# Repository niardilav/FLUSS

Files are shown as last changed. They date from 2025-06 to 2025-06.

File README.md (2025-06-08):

# Proyecto FLUSS
EL proyecto FLUSS busca investigar la viabilidad de turbinas tipo savonious de eje horizonal en los rios de montaña de colombia, y se busca desarrollar un prototipo de turbina para uso en laboratorio.

En este repositorio se encuentran los avances del proyecto FLUSS ganador de la convocatoria "Ingenio que transforma" 2024, cada carpeta corresponde a un desarrollo llevadoa a cabo durante la convocatoria, en las carpetas se pueden encontrar los archivos de códigos, modelos CAD y datos crudos de laboratorio.

A la fecha el proyecto se encuentra en desarrollo y se han logrado implementar pruebas de laboratorio para turbinas savonious en aire y se ha diseñado un banco de pruebas de generadores para caracterizar un motor stepper como generador.

## Participación en eventos cientificos

3 ponencias en el CIMM XII
- DISEÑO Y PROTOTIPADO DE UN TÚNEL DE VIENTO PARA PRUEBAS A ESCALA DE TURBINAS TIPO SAVONIUS. 
- CALIBRACIÓN Y USO DE GALGAS EXTENSIOMÉTRICAS.
- BANCO DE PRUEBAS PARA LA CARACTERIZACIÓN DE MOTORES COMO GENERADORES.

1 poster en expotech-UNAD 2025    
- Análisis del comportamiento de una turbina Savonius en condiciones de superficie libre.

# Integrantes del proyecto
Estudiantes

- Nicolás Ardila Vergara 
  Estudiante Ing Mecánica UNAL
  Lider del proyecto
  niardilav@unal.edu.co

- Mateo Velandia Suarez 
  Estudiante Ing Mecánica UNAL
  mavelandias@unal.edu.co
  
- Jairo David Diaz Luna
  Estudiante Ing Mecatrónica UNAL
  jdiazlu@unal.edu.co
  
- Maria Lucia Arias Ortiz
  Estudiante Ing Mecatrónica UNAL
  mariasor@unal.edu.co
  
- Laura Catalina Ramirez Villareal
  Estudiante Ing Mecánica UNAL
  laramirezvi@unal.edu.co
  
- Juan Jose Benavides Garreta
  Estudiante Ing Mecánica UNAL

- Juan Sebastian Moreno Gonzalez
  Estudiante Ing Electronica UNAL

- Jaime Andres Martín Moreno
  Estudiante Ing Mecatrónica UNAL

- Jonathan David Rodriguez Larrota
  Estudiante Ing Electrica UNAL

### Director del proyecto
Juan Miguel Mantilla Gonzalez
  jmmantillag@unal.edu.co
### Codirector del proyecto
Nestor Alonso Mancipe Muños

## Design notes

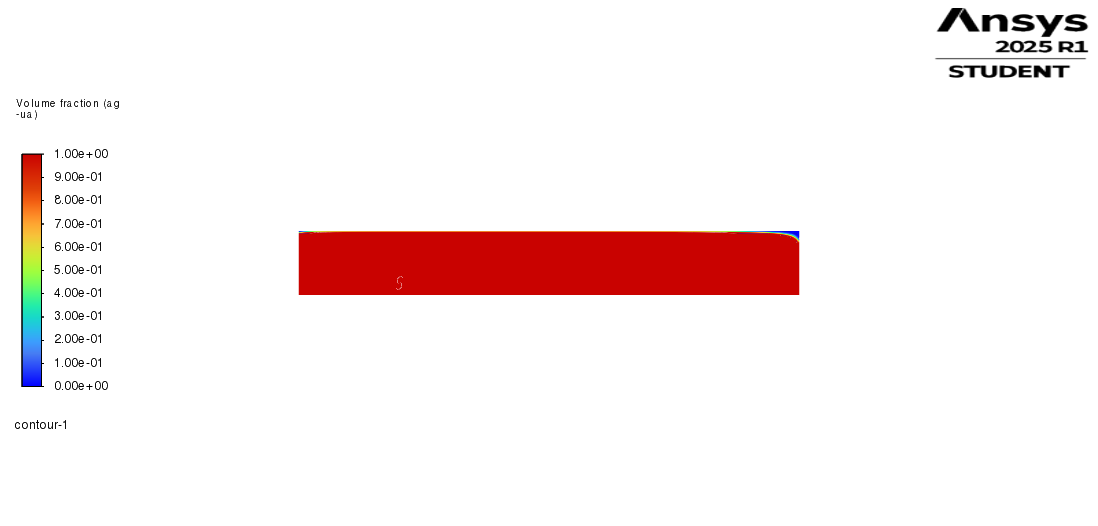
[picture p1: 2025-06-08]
Simulaciones_Canal_Hidraulica/Simulaciones_Ansys_y postproceso/turbina22_files/progress_files/dp0/FFF/Fluent/contour-1.png

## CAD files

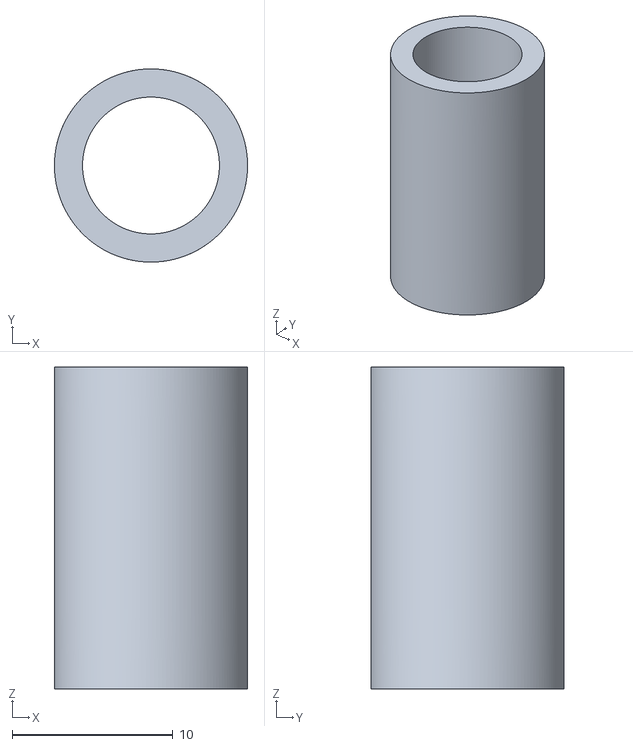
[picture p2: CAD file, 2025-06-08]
Pruebas_tunel_de_viento/Tunel_FLUSS/Modelos_inventor/Ensamble inercia/Camisa_eje.stl
12.0 x 12.0 x 20.0

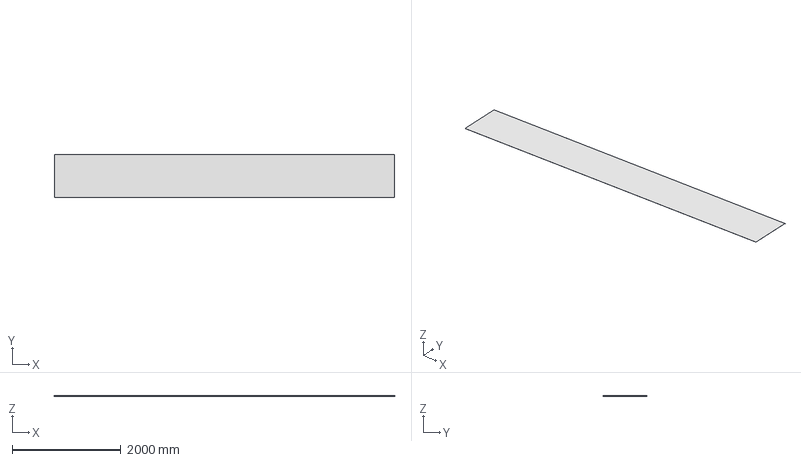
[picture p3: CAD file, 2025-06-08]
Simulaciones_Canal_Hidraulica/Simulaciones_Ansys_y postproceso/turbina22_files/import_files/TunelBasicoParte1norejas.stp
6260.0 x 800.0 x 1.00 mm

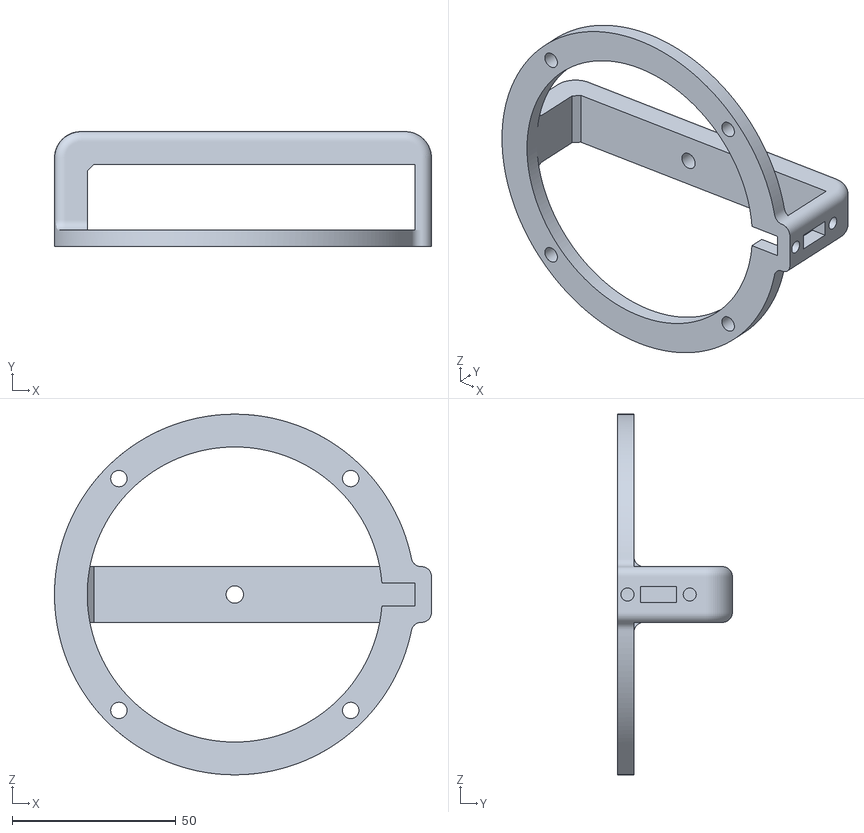
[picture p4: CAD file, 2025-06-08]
Pruebas_tunel_de_viento/Tunel_FLUSS/Modelos_inventor/Ensamble inercia/Soporte.stl
115.0 x 35.0 x 110.0

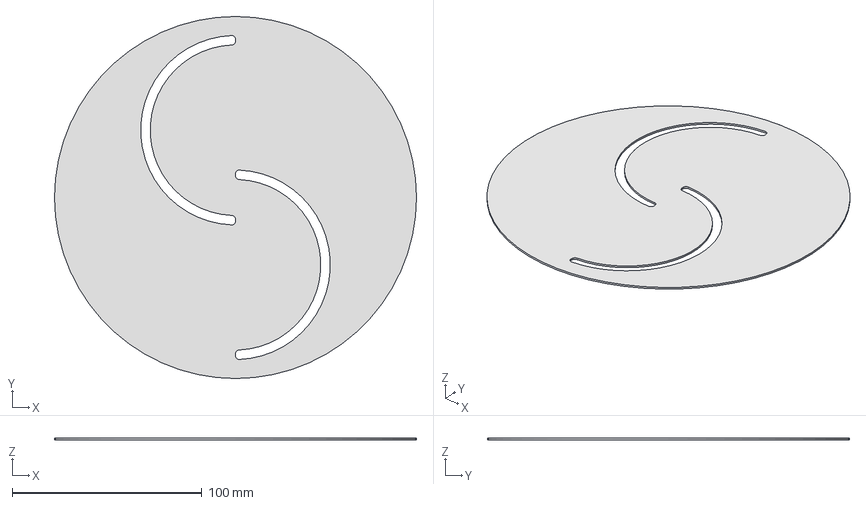
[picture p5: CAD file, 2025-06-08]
Simulaciones_Canal_Hidraulica/Simulaciones_Ansys_y postproceso/turbina22_files/import_files/TunelBasicoParte2.stp
191.0 x 191.0 x 1.00 mm

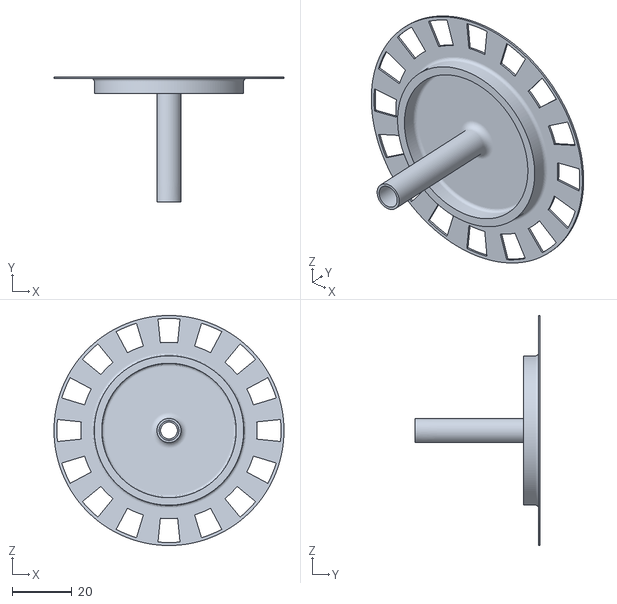
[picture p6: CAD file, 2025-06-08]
Pruebas_tunel_de_viento/Tunel_FLUSS/Modelos_inventor/Ensamble inercia/Eje_econder_V2.stl
77.0 x 42.0 x 77.0

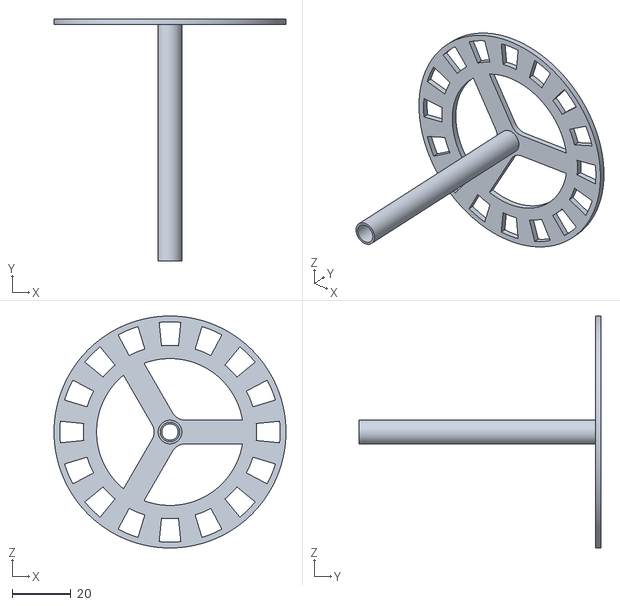
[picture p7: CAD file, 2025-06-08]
Pruebas_tunel_de_viento/Tunel_FLUSS/Modelos_inventor/Ensamble inercia/Eje_econder.stl
79.0 x 82.5 x 79.0

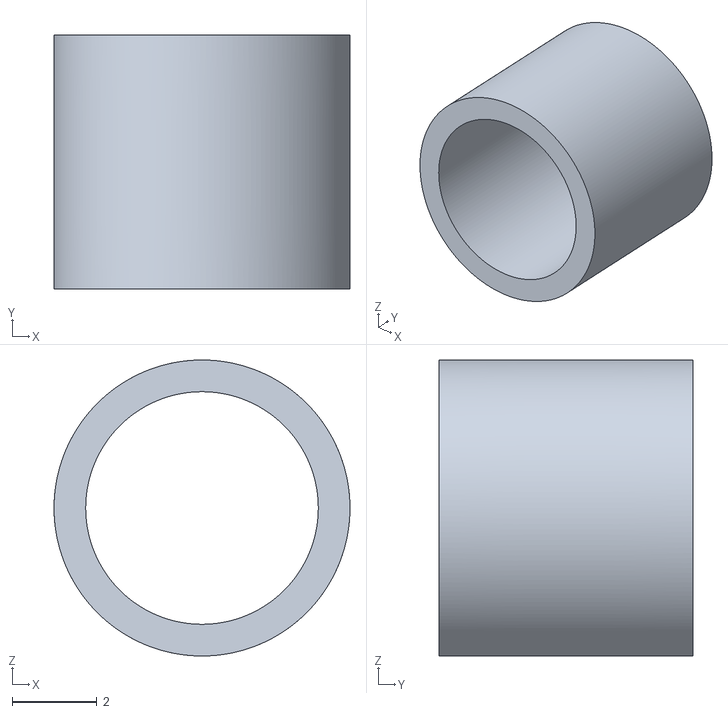
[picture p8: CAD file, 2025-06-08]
Pruebas_tunel_de_viento/Tunel_FLUSS/Modelos_inventor/Ensamble inercia/Buje_inercia.stl
7.00 x 6.00 x 7.00

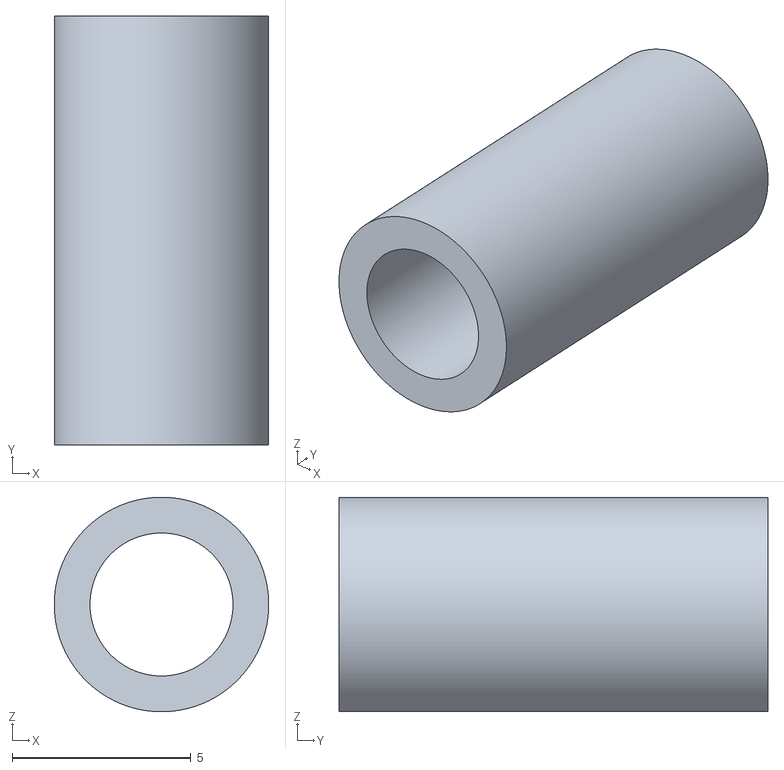
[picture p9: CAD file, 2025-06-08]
Pruebas_tunel_de_viento/Tunel_FLUSS/Modelos_inventor/Ensamble inercia/Poste_sensor.stl
6.00 x 12.0 x 6.00

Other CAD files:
Pruebas_tunel_de_viento/Tunel_FLUSS/Modelos_inventor/Ensamble inercia/Buje_inercia.ipt
Pruebas_tunel_de_viento/Tunel_FLUSS/Modelos_inventor/Ensamble inercia/Eje_econder.ipt
Pruebas_tunel_de_viento/Tunel_FLUSS/Modelos_inventor/Ensamble inercia/OldVersions/Eje_econder.0003.ipt
Pruebas_tunel_de_viento/Tunel_FLUSS/Modelos_inventor/Ensamble inercia/OldVersions/Prueba_ensamble inercia.0001.iam
Pruebas_tunel_de_viento/Tunel_FLUSS/Modelos_inventor/Ensamble inercia/OldVersions/Seccion_tunel.0001.ipt
Pruebas_tunel_de_viento/Tunel_FLUSS/Modelos_inventor/Ensamble inercia/OldVersions/Sensor.0002.ipt
Pruebas_tunel_de_viento/Tunel_FLUSS/Modelos_inventor/Ensamble inercia/OldVersions/Soporte.0001.ipt
Pruebas_tunel_de_viento/Tunel_FLUSS/Modelos_inventor/Ensamble inercia/OldVersions/soporte motor.0001.ipt
Pruebas_tunel_de_viento/Tunel_FLUSS/Modelos_inventor/Ensamble inercia/Part20.ipt
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

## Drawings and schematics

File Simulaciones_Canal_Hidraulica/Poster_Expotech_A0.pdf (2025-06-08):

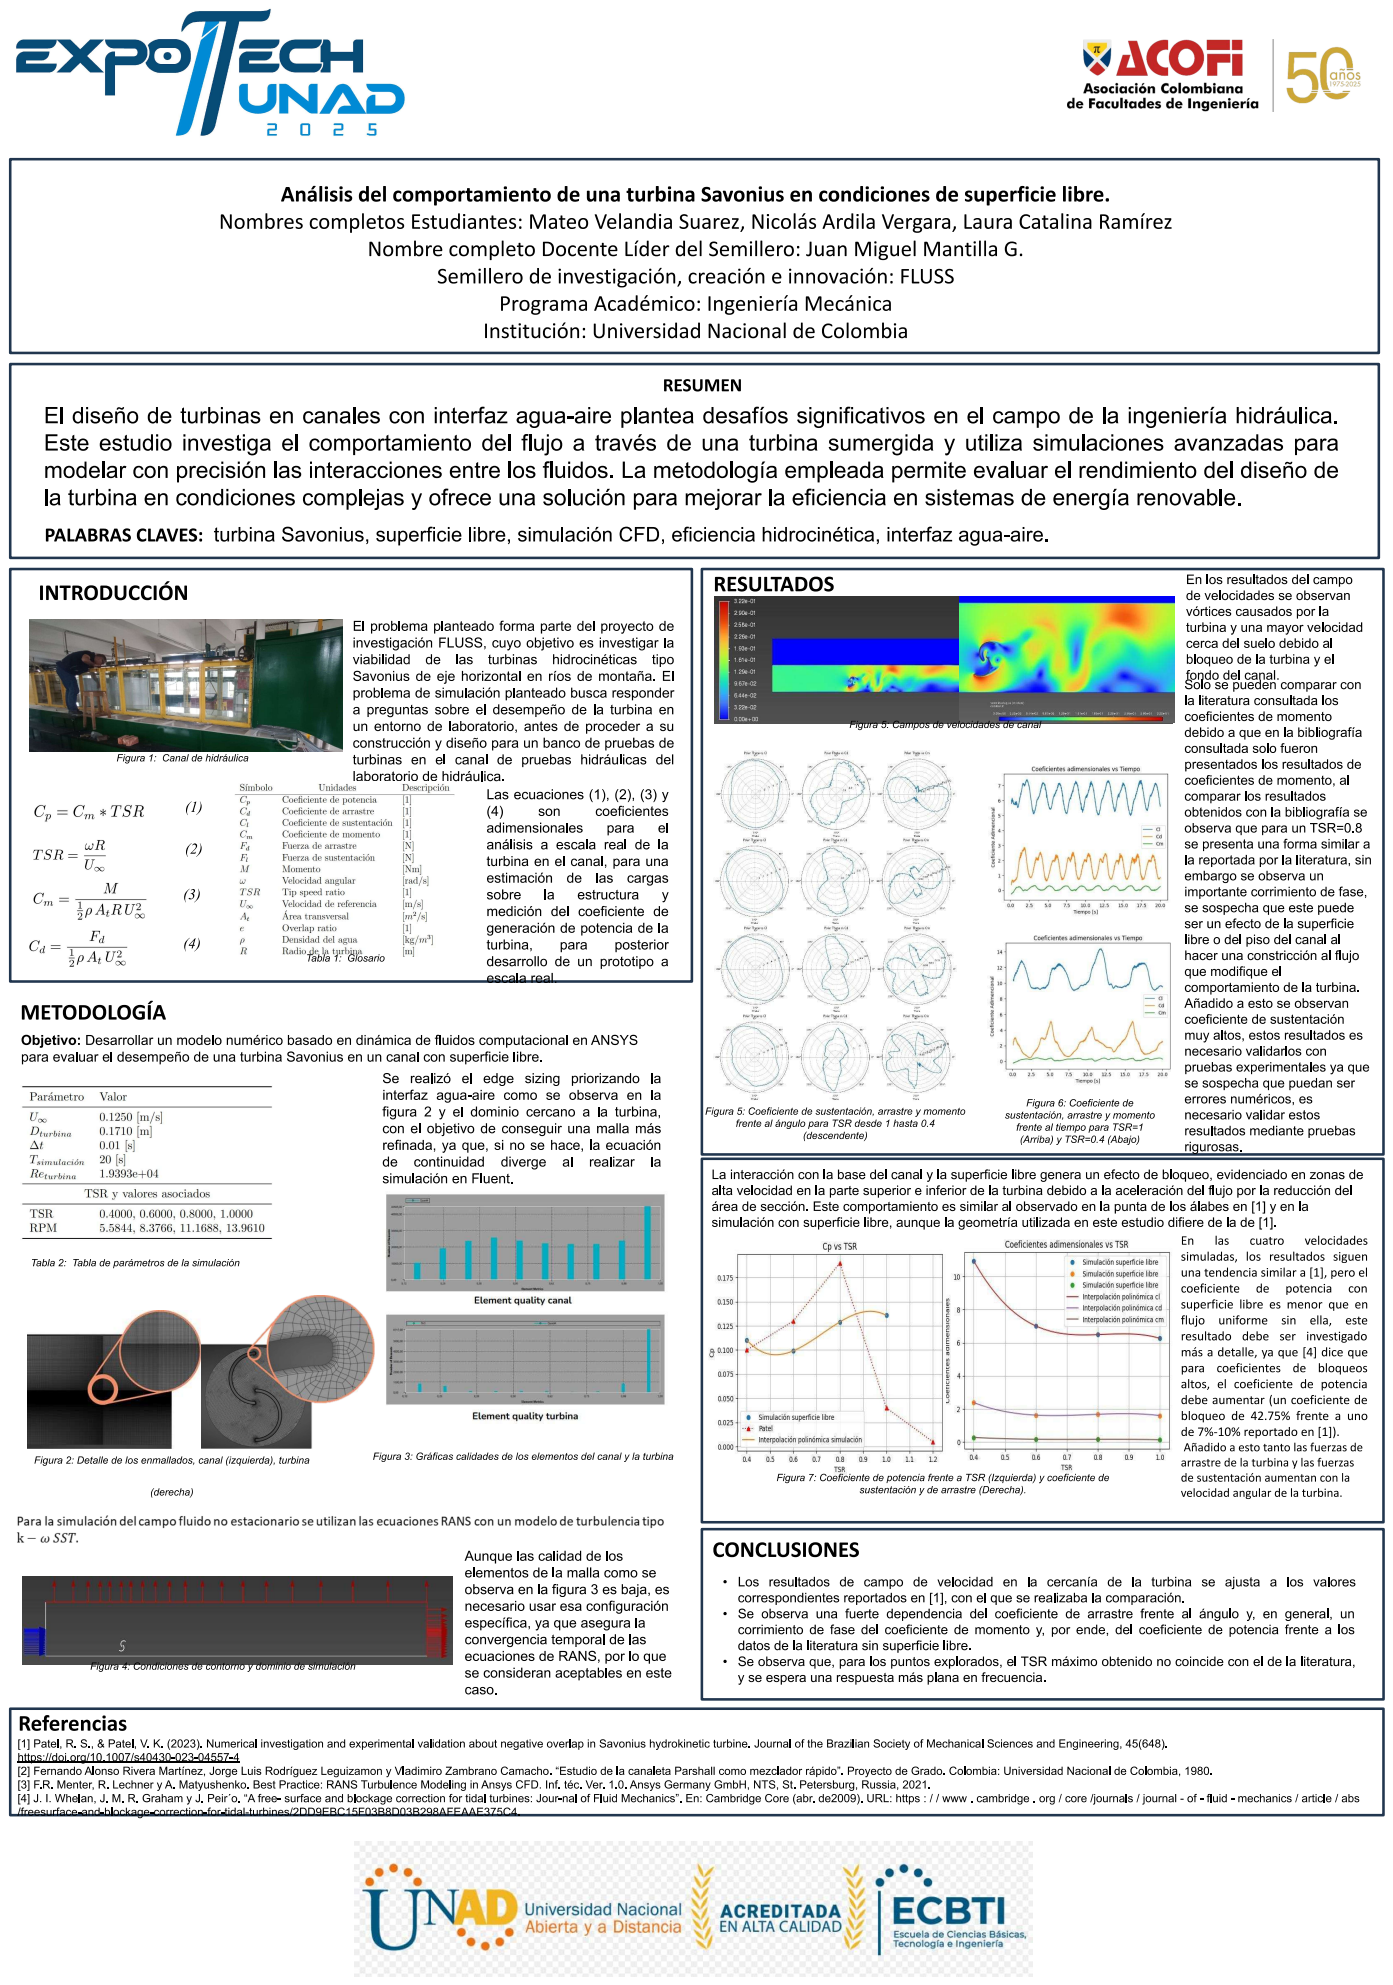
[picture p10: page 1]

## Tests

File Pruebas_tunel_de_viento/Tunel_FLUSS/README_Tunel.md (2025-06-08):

# Experimentos de similitud dimensional en tunel de viento
En esta carpeta se incluyen los diseños del tunel de viento de FLUSS, el trabajo presentado al CIMM y carpetas con datos crudos de pruebas de laboratorio junto con códigos de procesamiento de datos para la generación de las curvas de desempeño de la turbina.

Los datos crudos fueron generados en el tunel de viento propio para una turbina de 50mm de diametro, OR=-0.17 AR=1, y los settings del ESC del tunel fuerin 22V a 1.230 ms de Ton en la señal de PWM, en una fuente dual de 60W. La velocidad de viento medida oscila entre 7 y 8 m/s en la entrada de la turbina.

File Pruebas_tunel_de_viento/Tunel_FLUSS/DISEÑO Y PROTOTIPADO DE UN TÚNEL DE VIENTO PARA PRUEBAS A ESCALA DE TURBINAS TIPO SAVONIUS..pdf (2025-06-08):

## DISEÑO Y PROTOTIPADO DE UN TÚNEL DE VIENTO PARA

PRUEBAS A ESCALA DE TURBINAS TIPO SAVONIUS.

Nicolás Ardila Vergara, Mateo Velandia Suarez, Laura Catalina Ramírez Villarreal, Juan José Benavides Garreta, Maria Lucia Arias Ortiz, Jonathan David Rodriguez Larrota, Jaime Andrés Martín Moreno, Jairo David Diaz Luna, Juan Sebastian Moreno Gonzalez.

Proyecto “FLUSS” código Hermes (62804), Universidad Nacional de Colombia, Colombia. Núcleo Temático: Energías renovables y fuentes no convencionales.

### Introducción

En la actualidad es campo de investigación el uso de turbinas hidrocinéticas tipo savonius para la producción energética, ya sea para aprovechar la energía de ríos o ayudar a mitigar los efectos del cambio climático. Dado que la turbina está inmersa en un fluido, es necesario hacer todo el análisis hidrodinámico que esto conlleva. Por está razón el presente trabajo aborda el diseño y construcción de un túnel de viento, para la caracterización hidrodinámica de este tipo de turbinas.

Palabras clave: turbina, hidrocinética, savonius, túnel de viento.

### Métodos

Por simplicidad de construcción y las restricciones de espacio se decidió construir un túnel de viento tipo abierto de sección cuadrada, donde se incluye una admisión tobera, laminarizador, la sección de prueba y un difusor. El ventilador se encuentra en la parte posterior del difusor. El túnel tiene como objetivo en el corto plazo poder medir fuerzas de arrastre y en el futuro fuerzas de sustentación y momentos.
Para el diseño del túnel se usó la ecuación (1) para pérdidas menores y mayores para ductos, donde se tuvo en cuenta la longitud de la sección de prueba del túnel de viento, el difusor, la tobera, la admisión y el laminarizador.

Esto con el fin de evaluar el desempeño del túnel previo a su construcción y determinar los parámetros geométricos que permitan un mayor desempeño. Los parámetros para las pérdidas menores fueron tomados de [Karassik, 2004], [McGill, 2003], [White, 2004] y para la sección de prueba se utilizó el factor de fricción de Darcy para la rugosidad de maderas lisas [White, 2004].

En la Figura 1 se muestra la curva de desempeño del túnel de viento calculada y el punto de operación para el ventilador seleccionado a una

velocidad fija. Cómo ventilador se usó una hélice de avión de radio control propulsada por un motor

brushless por su alta relación entre potencia y tamaño.

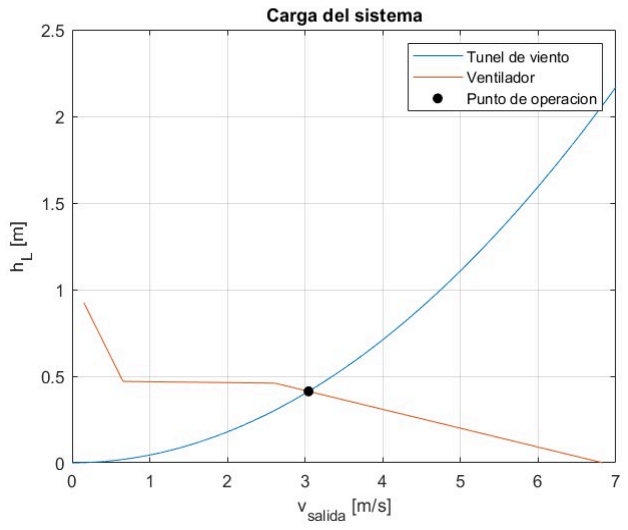
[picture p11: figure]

Figura 1: Punto de operación del sistema.

Para verificar el correcto funcionamiento del túnel se decidió realizar experimentos del coeficiente de arrastre de una geometría simple como lo es una esfera, visualizar el flujo con vapores de glicerina, y el perfil de velocidades dentro del túnel con un anemómetro de hilo caliente. Además se instalarán manómetros diferenciales de alcohol para medir las caídas de presiones en las secciones del túnel.

### Resultados

En la figura 2 se observa el primer prototipo del túnel de viento. El túnel tiene diferentes agujeros para inserción de aparatos de medición, En la sección de prueba se posiciona una celda de carga acoplada al soporte donde irá el objeto de prueba. En la parte de arriba del túnel se encuentra el sistema de control del motor y la celda de carga para la medición de la fuerza de arrastre.

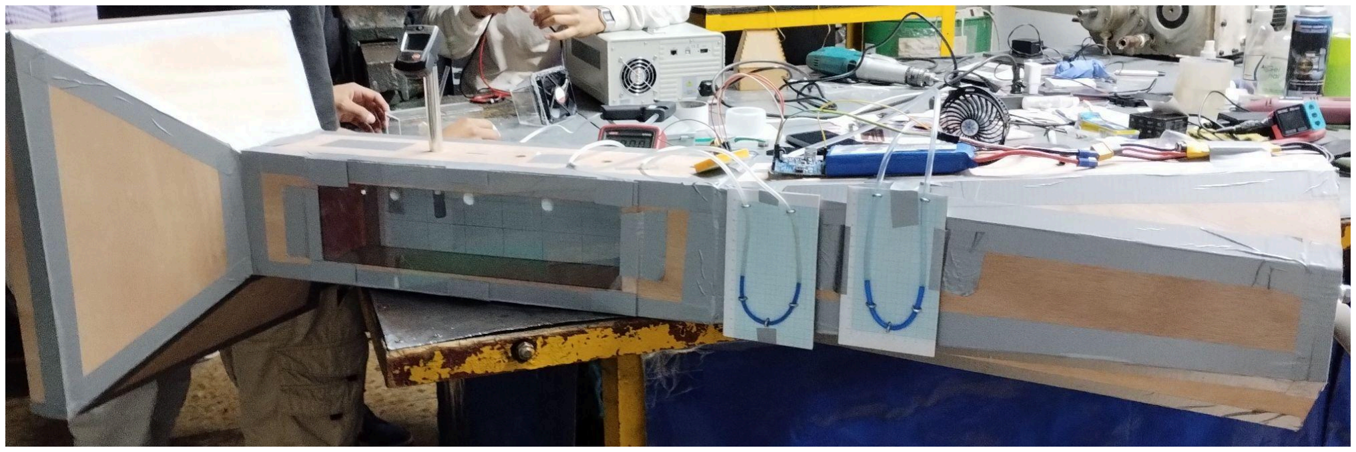
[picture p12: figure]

Figura 2: Primer prototipo del túnel de viento siendo calibrado.

En la figura 3 se observa las curvas resultado para coeficientes de arrastre teórico para una esfera lisa, los puntos obtenidos experimentalmente , y la curva de ajuste del resultado experimental.

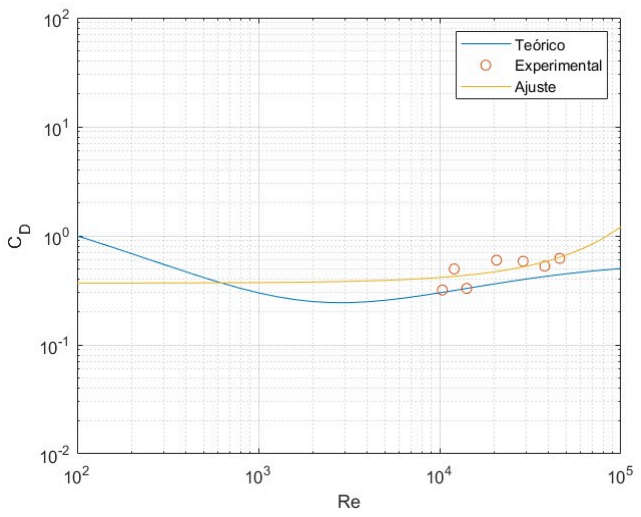
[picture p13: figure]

Figura 3: Coeficiente de arrastre contra número de Reynolds.

### Discusión

A las rangos de Reynolds medidos los datos de coeficiente de arrastre para la esfera se acercan a los teóricos, se observa una tendencia similar pero con arrastres mayores a la esfera lisa, esto es de esperar por la rugosidad inherente a la esfera real. Por lo tanto se verifica el correcto funcionamiento del túnel en el rango de números de Reynolds de
1x 10 a | .

4
4 x 10

4

El objetivo del túnel es modelar los coeficientes de arrastre, sustentación y momento para una turbina savonius que operará en un rango de números de
Reynolds entre 2. 2 x 10 a | el túnel fue

5
6 x 10

5
capaz de generar velocidades dentro de este rango pero se encuentra limitado por el tiempo de descarga de la batería del motor se espera realizar en el futuro más experimentos para validar el funcionamiento del túnel en este régimen de flujo, sin embargo si no fuera viable aumentar el rango de funcionamiento del túnel muchas geometrías presentan cambios significativos en sus coeficientes de arrastre y sustentación luego de Re > 10

4
[White, 2004], por lo cual no se descarta su uso para experimentación en las turbinas Savonius.

### Referencias

Karassik et al., Pump handbook, McGraw-Hill, 2004.

McGill, Duct System Design Guide, Air-Flow Corporation, 2003.

White et al., Mecánica de Fluidos, 5ta Edición, McGraw-Hill/Interamericana de España, S.A.U., 2004.

### Agradecimientos

Este trabajo fue financiado por la unidad de gestión de la innovación Ingnova de la Universidad Nacional de Colombia bajo la convocatoria Ingenio que transforma 2024, y a los docentes investigadores directores del Proyecto Fluss Juan Miguel Mantilla y Nestor Alonso Mancipe.

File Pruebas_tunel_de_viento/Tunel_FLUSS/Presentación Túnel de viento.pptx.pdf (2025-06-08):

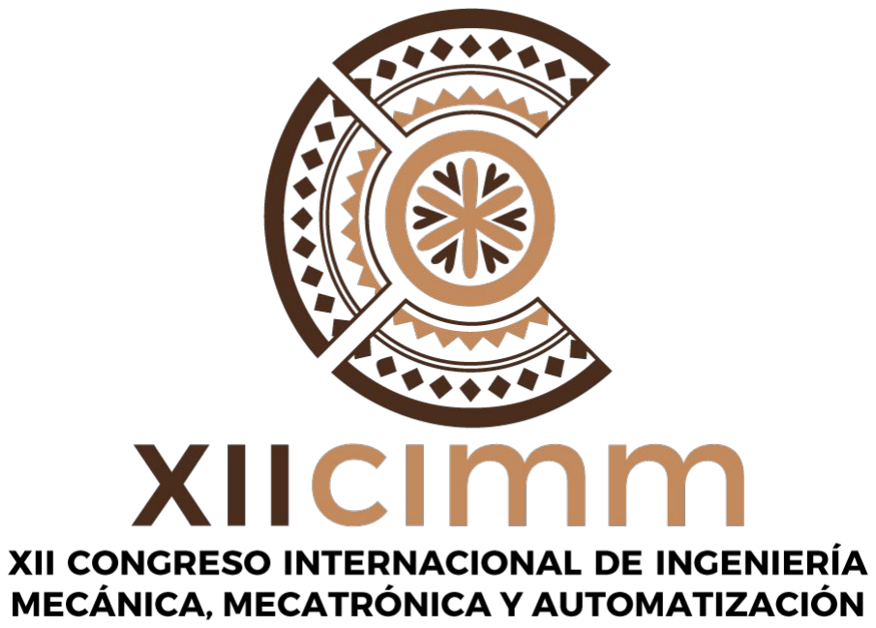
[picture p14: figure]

DISEÑO Y PROTOTIPADO DE UN TÚNEL DE VIENTO PARA PRUEBAS A ESCALA DE TURBINAS TIPO SAVONIUS

Autores:
Nicolas Ardila Vergara, Juan José Benavides Garreta, Laura Catalina Ramirez Villarreal, Mateo Velandia Suarez

Proyecto “FLUSS”
Código Hermes 62804

Universidad Nacional De Colombia, Colombia Núcleo Temático: Energías renovables y fuentes no convencionales.

INTRODUCCIÓN

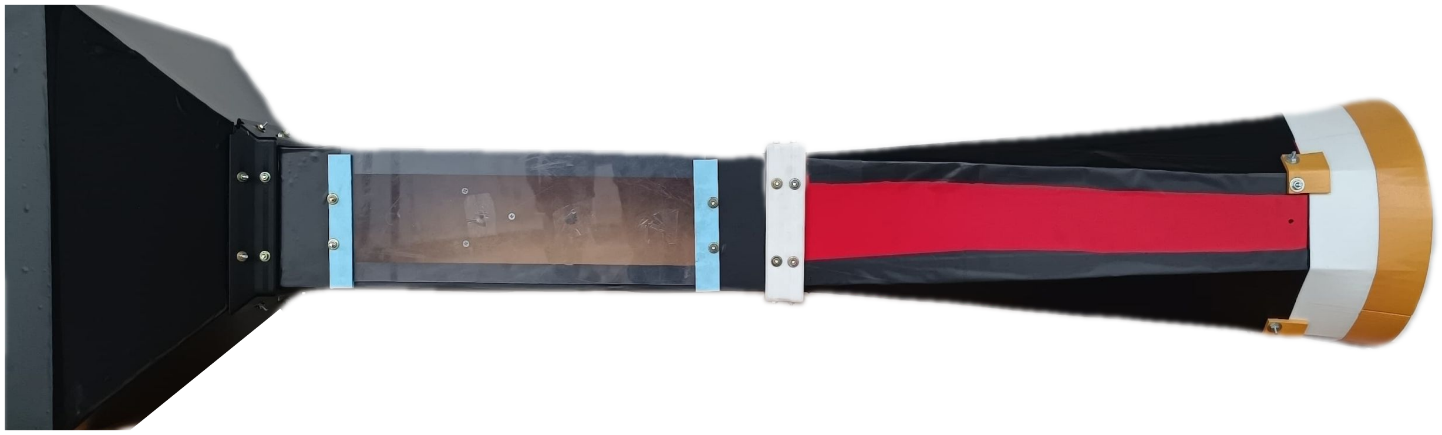
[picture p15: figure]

PROBLEMÁTICA

Con el fin de ahondar más a fondo la investigación de las turbinas tipo Savonius, se desarrolló un túnel de viento para la caracterización hidrodinámica de las mismas.

PALABRAS CLAVE:
Turbina, hidrocinética, savonius, túnel de viento.

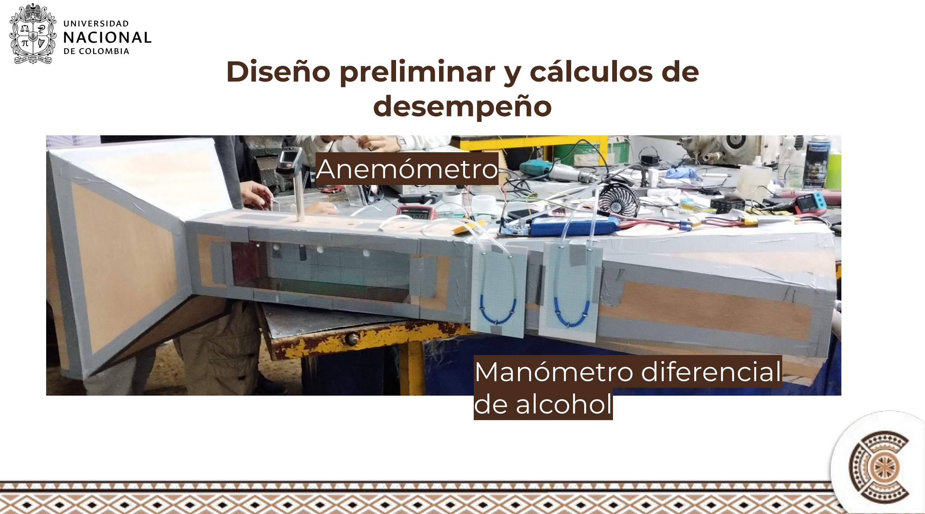
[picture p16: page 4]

Diseño preliminar y cálculos de desempeño

Anemómetro

Manómetro diferencial
de alcohol

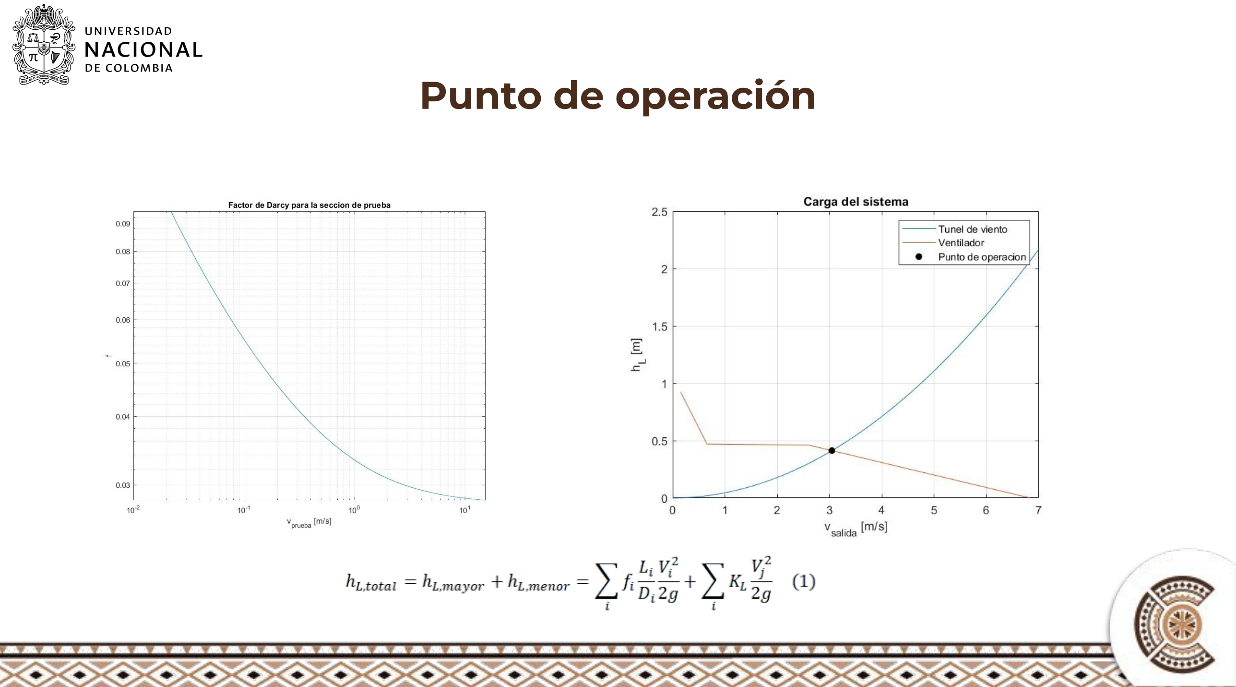
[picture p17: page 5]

Punto de operación

Capa limite

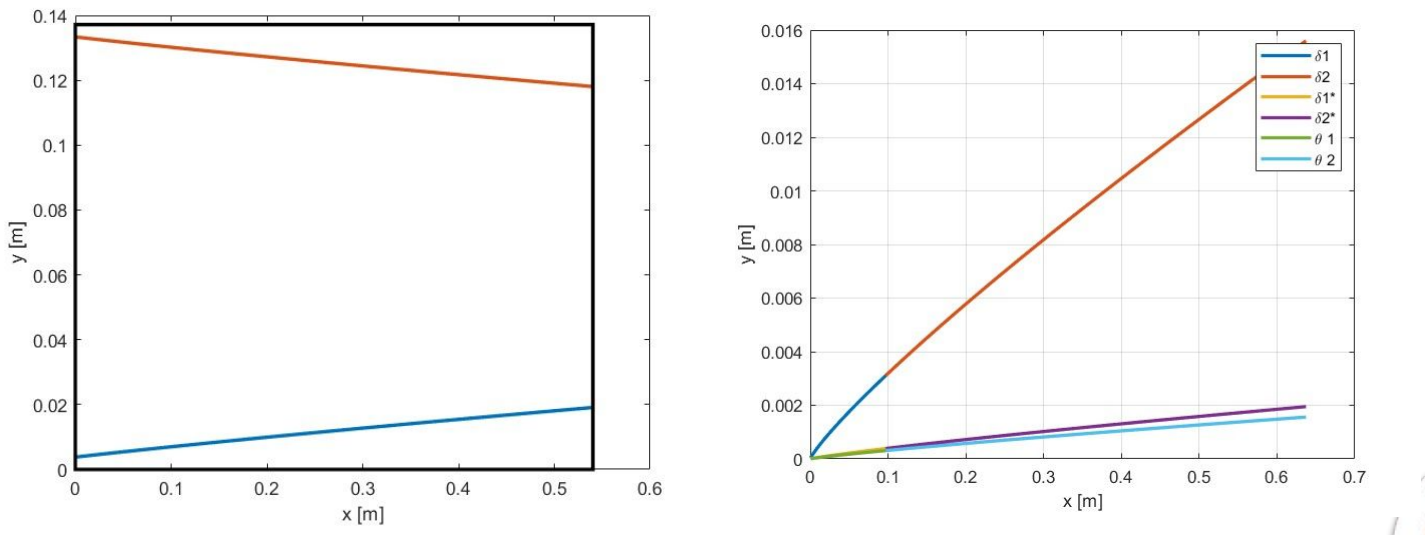
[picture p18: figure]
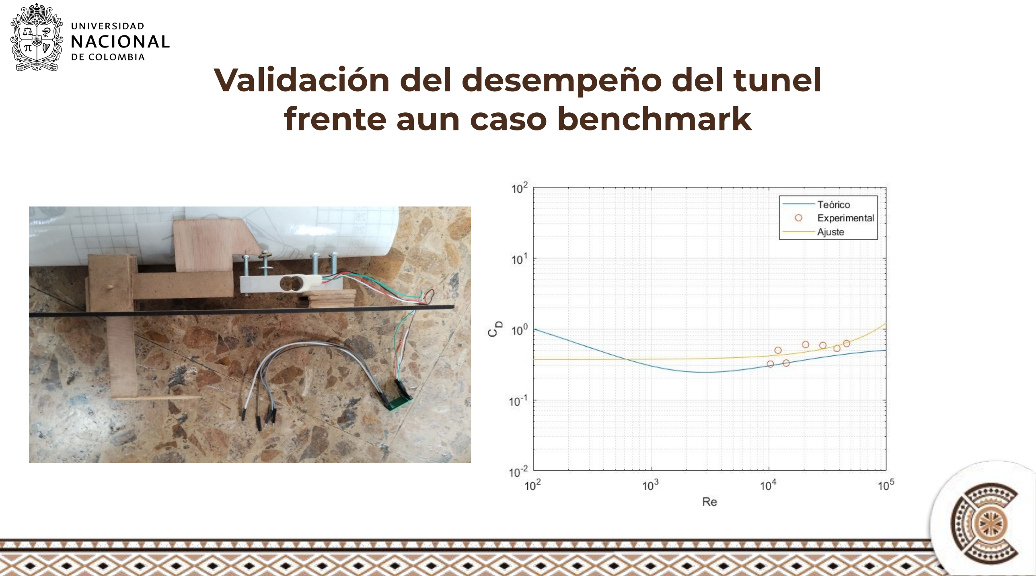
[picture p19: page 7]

Validación del desempeño del tunel frente aun caso benchmark

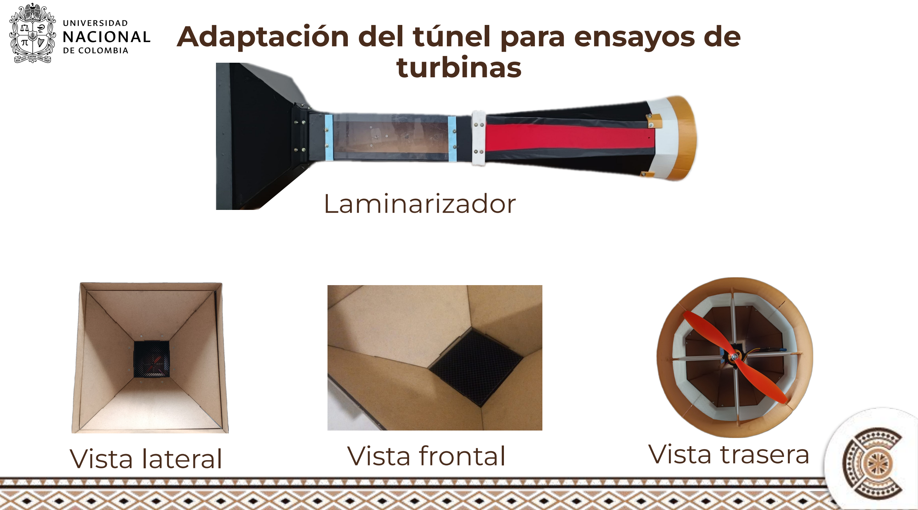
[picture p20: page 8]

Adaptación del túnel para ensayos de turbinas

Laminarizador

Vista lateral | Vista frontal | Vista trasera


Setup experimental

Osciloscopio

Generador de señales

Fuente de poder

Soporte motor


Montaje de la turbina

Turbinas savonius AR 1 ½ y ⅓ | Montaje de la turbina en el túnel


Refrigeración y modificación del ESC


Adaptación del túnel para funcionamiento

Rueda de inercia y encoder

Arduino para
adquisiscion de datos

Turbina en operación


Propuesta de modelo dinámico de la turbina

Propuesta de modelo dinámico de la turbina


Resultados
Primeros ensayos

https://youtu.be/QMdxYg5zm-o?si=KOCj9dZmcQfAikXl

https://youtu.be/QMdxYg5zm-o?si=dhmz1Cvq0xyAbkyk | https://youtu.be/QMdxYg5zm-o?si=KOCj9dZmcQfAikXl

Resultados
Primeros ensayos

https://youtu.be/QMdxYg5zm-o?si=KOCj9dZmcQfAikXl


https://youtu.be/KIURfHuR08Y?si=ImleQsb3eJ62W4uU&t=11


RESULTADOS


RESULTADOS
Operación del túnel


RESULTADOS
Primer ensayo de la turbina


RESULTADOS
Primer ensayo de la turbina


RESULTADOS
Primer ensayo de la turbina

RESULTADOS
Primer ensayo de la turbina


CONCLUSIONES

Se requieren más experimentos para poder trazar una curva más cercana a la teórica.

Se deben implementar sistemas para bajar la fricción con el objetivo de aumentar el TSR y poder trazar una región mayor de la curva.

Es necesario la implementación de un sistema de adquisición de datos con mayor frecuencia de muestreo.

TRABAJO A FUTURO

- Mejoras del sistema de adquisición de datos del túnel de viento.
- Utilización de una fuente de poder más potente para obtener velocidades más altas en el túnel de viento.
- Realizado de las curvas de desempeño de la turbina prototipo con corrección de fricción.

AGRADECIMIENTOS

Este trabajo fue financiado por la unidad de gestión de la innovación Ingnova de la Universidad Nacional de Colombia bajo la convocatoria Ingenio que transforma 2024, y a los docentes investigadores directores del Proyecto “Fluss” Juan Miguel Mantilla y Néstor Alonso Mancipe.

Contacto:
niardilav@unal.edu.co
+57 3187628596

REFERENCIAS


- J. B. Barlow, W. H. Rae Jr., and A. Pope, Low-Speed Wind Tunnel Testing, 3rd. John Wiley Sons, Inc., 1999.
- Karassik et al., Pump handbook, McGraw-Hill, 2004.
- McGill, Duct System Design Guide, Air-Flow Corporation, 2003.
- White et al., Mecánica de Fluidos, 5ta Edición, McGraw-Hill/Interamericana de España, S.A.U., 2004.

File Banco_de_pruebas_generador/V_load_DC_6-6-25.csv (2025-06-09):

Ohm @ 2ms-12V | Vload 1 | Vload 2 | Vload 3 | freq 1 | freq 2 | freq 3
100 | 13.77 | 13.43 | 13.36 | 2758 | 2764 | 2763
200 | 23.62 | 23.6 | 24.1 | 2650 | 2650 | 2647
300 | 30.11 | 29.75 | 29.72 | 2609 | 2610 | 2610
400 | 33.7 | 33.68 | 33.67 | 2602 | 2602 | 2601
500 | 36.37 | 36.35 | 36.35 | 2609 | 2608 | 2608
600 | 38.3 | 38.28 | 38.27 | 2619 | 2620 | 2620
700 | 39.71 | 39.72 | 39.72 | 2631 | 2632 | 2632
800 | 40.8 | 40.8 | 40.81 | 2640 | 2640 | 2640
900 | 41.68 | 41.7 | 41.69 | 2649 | 2649 | 2649
1000 | 42.46 | 42.46 | 42.26 | 2657 | 2657 | 2657

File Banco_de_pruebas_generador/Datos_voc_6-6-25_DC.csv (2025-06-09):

ms @ 12V | Voc 1 | Voc 2 | Voc 3 | freq 1 | freq 2 | freq 3
1.1 | 3.263 | 3.252 | 3.252 | 209 | 209 | 209.7
1.2 | 11.13 | 11.13 | 11.13 | 655 | 655 | 655
1.3 | 19.19 | 19.18 | 19.18 | 976 | 976 | 976
1.4 | 24.15 | 24.16 | 24.17 | 1286 | 1286 | 1286
1.5 | 33.68 | 33.59 | 33.78 | 1592 | 1592 | 1596
1.6 | 44.59 | 44.6 | 44.64 | 1890 | 1890 | 1891
1.7 | 57.3 | 57.4 | 57.3 | 2176 | 2176 | 2175
1.8 | 71.6 | 71.7 | 71.7 | 2454 | 2454 | 2454
1.9 | 83.6 | 83.7 | 83.7 | 2697 | 2698 | 2698
2 | 87.1 | 87.1 | 87.1 | 2776 | 2776 | 2776

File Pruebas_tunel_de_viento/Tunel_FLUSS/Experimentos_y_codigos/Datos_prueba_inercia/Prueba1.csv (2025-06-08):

#! | Workbook: | Custom | Custom
#! | Para reproducir estos datos: abra el archivo original de Excel | haga clic en el botón *Importar archivo de datos* de la pestaña *Secuencia de datos* de la cinta de opciones y desplácese hasta este archivo.
#! | Para obtener más información | visite http://aka.ms/hackingstem/
1902156 | 0
1902168 | 0
1902180 | 0
1902191 | 0
1902202 | 0
1902214 | 0
1902225 | 0
1902236 | 0
1902248 | 1
1902260 | 1
1902271 | 1
1902282 | 1
1902294 | 1
1902305 | 1
1902317 | 1
1902328 | 1
1902340 | 1
1902351 | 1
1902362 | 1
1902374 | 1
1902386 | 1
1902397 | 0
1902408 | 0
1902419 | 0
1902431 | 0
1902443 | 0
1902454 | 0
1902466 | 0
1902477 | 0
1902488 | 0
1902499 | 0
1902512 | 0
1902523 | 0
1902534 | 0
1902545 | 0
1902557 | 1
1902568 | 0
1902580 | 0
1902592 | 0
1902603 | 0
1902614 | 0
1902625 | 0
1902637 | 0
1902649 | 0
1902660 | 0
1902671 | 0
1902683 | 0
1902694 | 0
1902706 | 1
1902717 | 0
1902729 | 0
1902740 | 0
1902751 | 0
1902763 | 0
1902775 | 0
1902786 | 0
1902797 | 0
1902809 | 0
1902820 | 0
1902831 | 0
1902843 | 0
1902855 | 0
1902866 | 0
1902877 | 0
1902888 | 1
1902900 | 0
1902912 | 0
1902923 | 0
1902935 | 0
1902946 | 0
1902957 | 1
1902968 | 0
1902981 | 0
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

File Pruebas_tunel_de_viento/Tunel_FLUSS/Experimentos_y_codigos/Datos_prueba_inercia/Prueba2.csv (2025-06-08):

#! | Workbook: | Custom | Custom
#! | Para reproducir estos datos: abra el archivo original de Excel | haga clic en el botón *Importar archivo de datos* de la pestaña *Secuencia de datos* de la cinta de opciones y desplácese hasta este archivo.
#! | Para obtener más información | visite http://aka.ms/hackingstem/
2427584 | 0
2427595 | 0
2427608 | 0
2427619 | 0
2427630 | 0
2427641 | 0
2427653 | 0
2427665 | 0
2427676 | 0
2427687 | 0
2427699 | 0
2427710 | 0
2427721 | 0
2427734 | 0
2427745 | 0
2427756 | 0
2427767 | 0
2427779 | 0
2427790 | 0
2427802 | 0
2427813 | 0
2427825 | 0
2427836 | 0
2427847 | 0
2427858 | 0
2427871 | 0
2427882 | 0
2427893 | 0
2427905 | 0
2427916 | 0
2427927 | 0
2427939 | 1
2427951 | 1
2427962 | 0
2427973 | 0
2427984 | 0
2427997 | 0
2428008 | 0
2428019 | 0
2428030 | 0
2428042 | 0
2428053 | 0
2428065 | 0
2428077 | 0
2428088 | 0
2428099 | 0
2428110 | 0
2428122 | 0
2428134 | 1
2428145 | 1
2428156 | 0
2428168 | 0
2428179 | 0
2428190 | 0
2428203 | 0
2428214 | 0
2428225 | 0
2428236 | 1
2428248 | 0
2428259 | 0
2428271 | 0
2428282 | 0
2428294 | 0
2428305 | 0
2428316 | 0
2428327 | 1
2428340 | 0
2428351 | 0
2428362 | 0
2428374 | 0
2428385 | 0
2428397 | 0
2428408 | 1
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

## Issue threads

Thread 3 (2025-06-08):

Trazado de curvas con rectificador

niardilav, 2025-06-08:
Se debe trazar el comportamiento a circuito abierto del generador y la curva de carga realizada en laboratorio, copiar los datos del cuaderno a un .csv y generar las curvas necesarias, luego comparar con simulaciones si es posible.

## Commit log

2025-06-08 Actualización tunel de viento
    Se suben los primeros archivos del túnel de viento de fluss
    [Buje_inercia.ipt, Buje_inercia.stl, Camisa_eje.stl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]
2025-06-08 Simulaciones Ansys
    Se suben al repositorio las simulaciones de ansys de la turbina con movimiento prescrito
    [TunelBasicoParte1norejas.stp, TunelBasicoParte2.stp]
2025-06-09 Create V_load_DC_4-7-25.csv
    Datos de laboratorio de voltaje en carga resistiva
    [V_load_DC_4-7-25.csv]
2025-06-09 Datos generador
    Se añaden los archivos de pruebas del generador, y se trazaron las curvas para el circuito con rectificador
